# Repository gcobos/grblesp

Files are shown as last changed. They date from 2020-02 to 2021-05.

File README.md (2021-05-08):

# GRBLESP

Implements the latest version of GRBL using ESP8266 only, being able to connect by serial port, raw socket or websocket. 
To overcome the problem of the lack of pins, it uses SPI to drive 4 shift registers of 8 bits each. The aim of having
32 pins is to be able to handle up to 8 axis.

Interfaces
----------

For the raw socket connection, you can use pyserial, which supports it through "socket" protocol.
**socket://[IP_OF_ESP_DEVICE]:23**. It can be tested easily with [bCNC](https://github.com/vlachoudis/bCNC)

For the websocket connection, the url is: **ws://[IP_OF_ESP_DEVICE]:80/ws**

Wiring
------

- GPIO0 controls inputs as RESET, FEED_HOLD, START_CYCLE and SAFETY_DOOR

- GPIO2 controls all limits switches

- GPIO12 remains unused (because it functions as SPI HMISO)

- GPIO13 sends data to the shift registers (SPI HMOSI)

- GPIO14 clock signal for the shift registers (SPI HSCLK)

- GPIO15 serves as CHIP_SELECT for the SPI

The board should use 4 x 8-bit shift registers. They are arranged this way:
- 8 bits for step pins
- 8 bits for direction pins
- 8 bits for Misc, inputs and outputs, following this structure (although it might change still a bit):

  #define CONTROL_RESET_BIT         0  
  #define CONTROL_FEED_HOLD_BIT     1  
  #define CONTROL_CYCLE_START_BIT   2  
  #define CONTROL_SAFETY_DOOR_BIT   3  
  #define PROBE_BIT                 4  
  #define COOLANT_FLOOD_BIT         5  
  #define COOLANT_MIST_BIT          6    
  #define STEPPERS_DISABLE_BIT      7

- 8 bits for limits. All inputs

Probe, spindle, and probably other features, are not yet supported

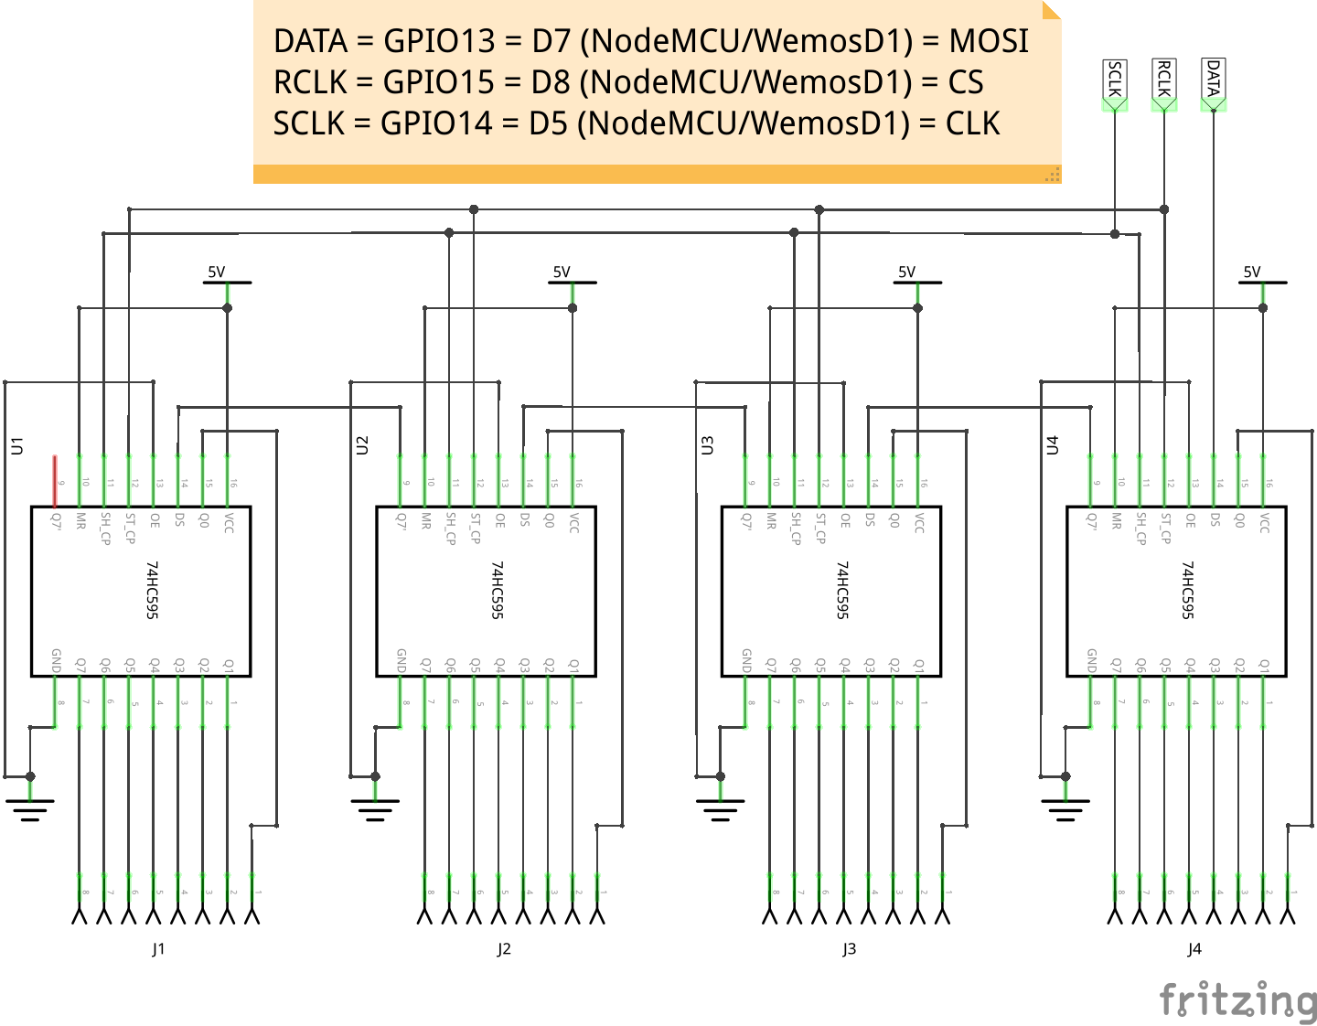
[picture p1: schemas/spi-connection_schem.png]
Connection diagram


#### J4
|Pin|Function|Type|
|-|-|-|
| 1 | STEP X | (output) |
| 2 | STEP Y | (output) |
| 3 | STEP Z | (output) |
| 4 | STEP A | (output) |
| 5 | STEP B | (output) |
| 6 | STEP C | (output) |
| 7 | STEP D | (output) |
| 8 | STEP E | (output) |

#### J3
|Pin|Function|Type|
|-|-|-|
| 1 | DIR X |(output) |
| 2 | DIR Y |(output) |
| 3 | DIR Z |(output) |
| 4 | DIR A |(output) |
| 5 | DIR B |(output) |
| 6 | DIR C |(output) |
| 7 | DIR D |(output) |
| 8 | DIR E |(output) |

#### J2
|Pin|Function|Type|
|-|-|-|
| 1 | RESET | (input) |
| 2 | FEED HOLD | (input) |
| 3 | CYCLE START | (input) |
| 4 | SAFETY DOOR | (input) |
| 5 | PROBE | (input) |
| 6 | COOLANT/FLOOD  |(output) |
| 7 | COOLANT/MIST  |(output) |
| 8 | STEPPERS_DISABLE |(output) |

#### J1
|Pin|Function|Type|
|-|-|-|
| 1 | LIMIT X | (input) |
| 2 | LIMIT Y | (input) |
| 3 | LIMIT Z | (input) |
| 4 | LIMIT A | (input) |
| 5 | LIMIT B | (input) |
| 6 | LIMIT C | (input) |
| 7 | LIMIT D | (input) |
| 8 | LIMIT E | (input) |

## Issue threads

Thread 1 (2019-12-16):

build error

xunni1000, 2019-12-16:
hello,
I made a build error.

> lib\grbl\src/grbl.hpp:42:27: fatal error: credentials.hpp: No such file or directory

```

> Executing task: C:\Users\xjw11\.platformio\penv\Scripts\platformio.exe run <

Warning! `lib_install` configuration option in section [env:esp07] is deprecated and will be removed in the next release! Please use `lib_deps` instead
Processing esp07 (platform: espressif8266; framework: arduino; board: esp12e)
------------------------------------------------------------------------------------------------------------------------------------------------------------------------------------------------------
Verbose mode can be enabled via `-v, --verbose` option
CONFIGURATION: https://docs.platformio.org/page/boards/espressif8266/esp12e.html
PLATFORM: Espressif 8266 2.3.1 > Espressif ESP8266 ESP-12E
HARDWARE: ESP8266 80MHz, 80KB RAM, 4MB Flash
PACKAGES: toolchain-xtensa 2.40802.191122 (4.8.2), tool-esptool 1.413.0 (4.13), tool-esptoolpy 1.20800.0 (2.8.0), framework-arduinoespressif8266 2.20602.191128 (2.6.2)
LDF: Library Dependency Finder -> http://bit.ly/configure-pio-ldf
LDF Modes: Finder ~ chain, Compatibility ~ soft
Found 36 compatible libraries
Scanning dependencies...
Dependency Graph
|-- <ArduinoJson> 6.13.0
|-- <ESP Async WebServer> 1.2.3
|   |-- <ESPAsyncTCP> 1.2.2
|   |   |-- <ESP8266WiFi> 1.0
|   |-- <Hash> 1.0
|   |-- <ESP8266WiFi> 1.0
|   |-- <ArduinoJson> 6.13.0
|-- <grbl>
|   |-- <SPI> 1.0
|   |-- <EEPROM> 1.0
|   |-- <ESPAsyncTCP> 1.2.2
|   |   |-- <ESP8266WiFi> 1.0
|   |-- <ArduinoOTA> 1.0
|   |   |-- <ESP8266WiFi> 1.0
|   |   |-- <ESP8266mDNS> 1.2
|   |   |   |-- <ESP8266WiFi> 1.0
|   |-- <ESP8266WiFi> 1.0
|   |-- <ESP Async WebServer> 1.2.3
|   |   |-- <ESPAsyncTCP> 1.2.2
|   |   |   |-- <ESP8266WiFi> 1.0
|   |   |-- <Hash> 1.0
|   |   |-- <ESP8266WiFi> 1.0
|   |   |-- <ArduinoJson> 6.13.0
|   |-- <ESP8266mDNS> 1.2
|   |   |-- <ESP8266WiFi> 1.0
|   |-- <Ticker> 1.0
Building in release mode
Compiling .pio\build\esp07\src\main.cpp.o
Compiling .pio\build\esp07\lib98f\ESP8266WiFi\BearSSLHelpers.cpp.o
Compiling .pio\build\esp07\lib98f\ESP8266WiFi\CertStoreBearSSL.cpp.o
Compiling .pio\build\esp07\lib98f\ESP8266WiFi\ESP8266WiFi.cpp.o
Compiling .pio\build\esp07\lib98f\ESP8266WiFi\ESP8266WiFiAP.cpp.o
Compiling .pio\build\esp07\lib98f\ESP8266WiFi\ESP8266WiFiGeneric.cpp.o
Compiling .pio\build\esp07\lib98f\ESP8266WiFi\ESP8266WiFiMulti.cpp.o
Compiling .pio\build\esp07\lib98f\ESP8266WiFi\ESP8266WiFiSTA-WPS.cpp.o
In file included from src\main.cpp:23:0:
lib\grbl\src/grbl.hpp:42:27: fatal error: credentials.hpp: No such file or directory

***********************************************************************
* Looking for credentials.hpp dependency? Check our library registry!
*
* CLI  > platformio lib search "header:credentials.hpp"
* Web  > https://platformio.org/lib/search?query=header:credentials.hpp
*
***********************************************************************

 #include "credentials.hpp"
                           ^
compilation terminated.
*** [.pio\build\esp07\src\main.cpp.o] Error 1
===================================================================================== [FAILED] Took 3.19 seconds =====================================================================================
```

apollo2030, 2020-01-21:
Same here

gcobos, 2020-01-24:
Closing this issue now, as it was solved.

Closed 2020-01-24.

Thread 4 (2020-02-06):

Soft WDT reset when sending "?" or "x1y1z1" commands

apollo2030, 2020-02-06:
After compiling and flashing grblesp to the NodeMcu board once the `?` is sent via the serial monitor the board responds with the status string then it software resets.

The same thing happens once a command lile `x1y1z1` is sent to the board. In this case only the `x1` motion is executed followed by a software reset.

While sending the `$` or `$#` commands no reset is happening.

gcobos, 2020-02-06:
I removed my ".platformio" folder and suddenly I started having the same WDT problems, so merging. Thanks!

Closed 2020-02-06.

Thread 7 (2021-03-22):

steppers pause when send gcode via websocket

MillerRen, 2021-03-22:
hi @gcobos thank you  create this great object. It works fine by usb serial but websocket. Steppers always paused and run agin later. I gess maybe the timer0 issue. Timer0 used by wifi feature,but steppers pluse used timer0 too. Have you faced this problem?

gcobos, 2021-03-23:
Hi! Thanks for trying this out. The support for websockets is not fully tested. What are you using as the client for websocket?

MillerRen, 2021-03-24:
lasergrbl

gcobos, 2021-03-26:
Thanks, I'll check it out on the weekend

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

gcobos, 2021-03-28:
I would recommend to not to use this project with lasergrbl. Many of the fuctionalities of GRBL are not enabled, and only the motor control is ensured to work. I would choose something like https://github.com/bdring/Grbl_Esp32 which has much more support, but you will then need an ESP32, instead of a ESP8266

MillerRen, 2021-03-30:
Thank you for your advice. I am porting this to a pen plotter or laser engraver. Esp8266 has enough pins. It's a nice things that a 2 axis cnc powered by esp8266 without external ic. Because esp8266 is cheap and simple :-)

Closed 2021-03-30.

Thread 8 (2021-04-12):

Core xy

qiwalker, 2021-04-12:
Hi,

Can i use esp32 ?
And is iy able to configure corexy machine ?

Thanks

gcobos, 2021-04-13:
I haven't tried with CoreXY configuration, but I wouldn't recommend it. But you may try this other project. It is much more mature and it works with the ESP32 directly. https://github.com/bdring/Grbl_Esp32

Closed 2021-04-14.

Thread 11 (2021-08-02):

how do I connect limit switches with 3 pins

psyqjo, 2021-08-02:
how do i connect limit switches with 3 pins that have 5v gnd and signal? and is the stepper disable pin connected to enable on the stepper driver? unfortunately this is not visible on the schematic sketch.

gcobos, 2021-08-15:
Hi! I should add that part to the schematic at some point. GPIO2 (D4 in NodeMCU) controls all the limits. You need to connect D4 to the switch and to 3V through a pull up resistor. Then the other wire of the switch must be connected to the pin from the shift registers controlling the corresponding limit for the axis.

And yes, the ENABLE pin is to ENABLE/DISABLE the stepper drivers.

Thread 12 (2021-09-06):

error: no matching function for call to 'min(double, float)'

couto0, 2021-09-06:
When compiling the project without changing anything, I've got the following error:
```lib/grbl/src/nuts_bolts.cpp:161:79: error: no matching function for call to 'min(double, float)'```

I'm using VSCode with PlatformIO `v2.3.3`

Based on  https://github.com/RobTillaart/Arduino/issues/128 I was able to solve the error by changing `lib/grbl/src/nuts_bolts.cpp:161`

from
```c++
 limit_value = min((double)limit_value,fabs(max_value[idx]/unit_vec[idx]));
```

to
```c++
 limit_value = _min((double)limit_value,fabs(max_value[idx]/unit_vec[idx]));
```

Closed 2022-01-13.

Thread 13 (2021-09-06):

missing semicolon in lib/grbl/src/stepper.cpp

couto0, 2021-09-06:
In `lib/grbl/src/stepper.cpp:543:36` there is a missing semicolon that prevents the project from compiling.

Closed 2021-09-19.

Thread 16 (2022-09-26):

Pins and GPIO

Kraiye, 2022-09-26:
Please advise where I can find the shift register or how to alter the pins to match an arduino uno.
I'm using a WeMos D1 board and need the standard Arduino GPIO arrangement.

gcobos, 2022-09-27:
Hi! Shift registers are extra chips that have to be placed on a board, to make ESP8266 have enough pins to handle up to 8 axis. I don't think it's worth to try to match the pin arrangement in the Arduino, it's better idea to just get an Arduino to do the job.

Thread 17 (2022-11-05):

Unipolar Motor Support

Francall01, 2022-11-05:
Hi

Does this support unipolar stepper motors such as 28byj-48  ?

Many thanks.

gcobos, 2022-11-06:
Hi! I would recommend to transform those unipolar motors into bipolar. It's a much simpler and cheaper method than trying to modify GRBL for it to work. Here is a video about how to do it. https://youtu.be/FLJGCZslOcM?t=102

Closed 2022-11-06.

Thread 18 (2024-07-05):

Not compiling with latest esp core and PIO

Algtronic, 2024-07-05:
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
I dunno what is causing the issue (XCHAL_INSTRAM1_VADDR is defined), but project is not compiling.

Algtronic, 2025-01-19:
Thanks! I already fixed that temporarily - inserted values myself. Something weird happened to my PIO environment.

gcobos, 2025-05-10:
I have now updated platformio.ini to pin platform and libraries to working versions

Closed 2025-05-10.

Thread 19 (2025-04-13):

error help

sasan18s, 2025-04-13:
hi . iam test  it with platform io and arduino ide and in theme after verify got error :
platform io:
[{
	"resource": "/c:/Users/Sasan/platformgit/grblesp/lib/grbl/src/nuts_bolts.hpp",
	"owner": "cpp",
	"severity": 8,
	"message": "expected unqualified-id before '(' token",
	"startLineNumber": 57,
	"startColumn": 18,
	"endLineNumber": 57,
	"endColumn": 18
}]
arduino ide :
expected unqualified-id before '(' token
for line :
#define max(a,b) (((a) > (b)) ? (a) : (b))
#define min(a,b) (((a) < (b)) ? (a) : (b))
help please
iam just want control two XY stepper for diy Laser machine and think Maybe It work .

sasan18s, 2025-04-16:
؟؟

gcobos, 2025-04-16:
Hi! It's probably because "min" and "max" is already defined somewhere else. Did you tried just commenting those two lines?

// #define max(a,b) (((a) > (b)) ? (a) : (b))
// #define min(a,b) (((a) < (b)) ? (a) : (b))

sasan18s, 2025-04-17:
yeah I test It and the it error in
Cpu_map File in :

  #define CONTROL_INPUT_GPIO_PIN    D3    // GPIO_0 = D3

  #define LIMIT_INPUT_GPIO_PIN    D4    // GPIO_2 = D4

error :

'D3' was not declared in this scope
'D4' was not declared in this scope

and I just turn D3 to 3 - D4 to 4 like that :

  #define CONTROL_INPUT_GPIO_PIN    3    // GPIO_0 = D3

  #define LIMIT_INPUT_GPIO_PIN    4    // GPIO_2 = D4

 and it Errored :

Error compiling for board Generic ESP8266 Module.

and if i comment this lines too :
//  #define CONTROL_INPUT_GPIO_PIN    D3    // GPIO_0 = D3

//  #define LIMIT_INPUT_GPIO_PIN    D4    // GPIO_2 = D4

it error :

'LIMIT_INPUT_GPIO_PIN' was not declared in this scope

for line :

        if (!GPIP(LIMIT_INPUT_GPIO_PIN)) {
in limits.cpp ...

what should i do ?

sasan18s, 2025-04-17:
i think esp dip name should be like that :
                  '    static const uint8_t D0   = 16;',
                  '    static const uint8_t D1   = 5;',
                  '    static const uint8_t D2   = 4;',
                  '    static const uint8_t D3   = 0;',
                  '    static const uint8_t D4   = 2;',
                  '    static const uint8_t D5   = 14;',
                  '    static const uint8_t D6   = 12;',
                  '    static const uint8_t D7   = 13;',
                  '    static const uint8_t D8   = 15;',
                  '    static const uint8_t D9   = 3;',
                  '    static const uint8_t D10  = 1;',
 iam find it in boards.txt in esp8266 folder in arduino library .

gcobos, 2025-05-10:
I'm trying myself to compile the whole package, not having much success. There's a mess with Arduino dependencies, and AsyncTCPWebServer libraries, mixing ESP32 and RP240 in the mix.

I'm trying to find the cleanest way to make it compile, probably requiring to fix versions of packages and libraries to older versions.

Basically, AsyncTCP is focusing on ESP32 and dropping compatibility with ESP8266, so it's going to get more and more difficult.

gcobos, 2025-05-10:
I have updated the project, fixing versions of platform and libraries to working ones.

Closed 2025-05-10.

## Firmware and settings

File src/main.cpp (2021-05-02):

/*
  main.c - An embedded CNC Controller with rs274/ngc (g-code) support
  Part of Grbl

  Copyright (c) 2011-2016 Sungeun K. Jeon for Gnea Research LLC
  Copyright (c) 2009-2011 Simen Svale Skogsrud

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
  You should have received a copy of the GNU General Public License
  along with Grbl.  If not, see <http://www.gnu.org/licenses/>.
*/

#include <Arduino.h>
#include "grbl.hpp"

// Declare system global variable structure
system_t sys;
int32_t sys_position[N_AXIS];      // Real-time machine (aka home) position vector in steps.
int32_t sys_probe_position[N_AXIS]; // Last probe position in machine coordinates and steps.
volatile uint8_t sys_probe_state;   // Probing state value.  Used to coordinate the probing cycle with stepper ISR.
volatile uint8_t sys_rt_exec_state;   // Global realtime executor bitflag variable for state management. See EXEC bitmasks.
volatile uint8_t sys_rt_exec_alarm;   // Global realtime executor bitflag variable for setting various alarms.
volatile uint8_t sys_rt_exec_motion_override; // Global realtime executor bitflag variable for motion-based overrides.
volatile uint8_t sys_rt_exec_accessory_override; // Global realtime executor bitflag variable for spindle/coolant overrides.
#ifdef DEBUG
  volatile uint8_t sys_rt_exec_debug;
#endif

void setup(void){
  // Initialize system upon power-up.
  serial_init();    // Setup serial connection
  eeprom_init();		// Initialize EEPROM
  settings_init();  // Load Grbl settings from EEPROM
  stepper_init();   // Configure stepper pins and interrupt timers
  system_init();    // Configure pinout pins and pin-change interrupt

  memset(sys_position,0,sizeof(sys_position)); // Clear machine position.
  sei(); // Enable interrupts

  // Initialize system state.
  #ifdef FORCE_INITIALIZATION_ALARM
    // Force Grbl into an ALARM state upon a power-cycle or hard reset.
    sys.state = STATE_ALARM;
  #else
    sys.state = STATE_IDLE;
  #endif

  // Check for power-up and set system alarm if homing is enabled to force homing cycle
  // by setting Grbl's alarm state. Alarm locks out all g-code commands, including the
  // startup scripts, but allows access to settings and internal commands. Only a homing
  // cycle '$H' or kill alarm locks '$X' will disable the alarm.
  // NOTE: The startup script will run after successful completion of the homing cycle, but
  // not after disabling the alarm locks. Prevents motion startup blocks from crashing into
  // things uncontrollably. Very bad.
  #ifdef HOMING_INIT_LOCK
    if (bit_istrue(settings.flags,BITFLAG_HOMING_ENABLE)) { sys.state = STATE_ALARM; }
  #endif

  #ifdef ENABLE_WIFI
    wifi_init();
  #endif
}

void loop(void)
{
  // Grbl initialization loop upon power-up or a system abort. For the latter, all processes
  // will return to this loop to be cleanly re-initialized.

  // Reset system variables.
  uint8_t prior_state = sys.state;
  memset(&sys, 0, sizeof(system_t)); // Clear system struct variable.
  sys.state = prior_state;
  sys.f_override = DEFAULT_FEED_OVERRIDE;  // Set to 100%
  sys.r_override = DEFAULT_RAPID_OVERRIDE; // Set to 100%
  sys.spindle_speed_ovr = DEFAULT_SPINDLE_SPEED_OVERRIDE; // Set to 100%
	memset(sys_probe_position,0,sizeof(sys_probe_position)); // Clear probe position.
  sys_probe_state = 0;
  sys_rt_exec_state = 0;
  sys_rt_exec_alarm = 0;
  sys_rt_exec_motion_override = 0;
  sys_rt_exec_accessory_override = 0;

  // Reset Grbl primary systems.
  serial_reset_read_buffer(CLIENT_ALL); // Clear serial read buffer
  gc_init(); // Set g-code parser to default state
  spindle_init();
  coolant_init();
  limits_init();
  probe_init();
  plan_reset(); // Clear block buffer and planner variables
  st_reset(); // Clear stepper subsystem variables.

  // Sync cleared gcode and planner positions to current system position.
  plan_sync_position();
  gc_sync_position();

  // Print welcome message. Indicates an initialization has occured at power-up or with a reset.
  report_init_message(CLIENT_ALL);

  // Start Grbl main loop. Processes program inputs and executes them.
  protocol_main_loop();
}

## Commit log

2018-07-04 Almost working, using Wemos D1 board
2018-08-06 Add SPI.write to pulse steppers
2019-11-08 Handle control inputs (reset, hold, cycle start, ...) using GPIO0
    [main.cpp]
2019-11-23 Some details about pin use
2020-02-02 Added some more details about wiring
    [spi-connection.fzz]
2020-02-02 Details about wiring
2020-02-06 Enable interrupts after the task switch flag was cleared
2021-05-02 Support for socket connetion + improvements
2021-05-08 Handle socket disconnection and fix parameter report
2021-05-11 Keep shift registers at 1/4 of the ESP speed, as their max speed at 5V is normally about 25Mhz
2021-05-16 Adjusting timers
2021-06-12 Fixes timing issuesand adds the possibility to use DC motors in every axis
2022-01-09 Fix prescaler for timer1 and enable AMASS by default

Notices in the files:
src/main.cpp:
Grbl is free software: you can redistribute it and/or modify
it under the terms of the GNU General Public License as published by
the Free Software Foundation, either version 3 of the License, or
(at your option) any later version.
